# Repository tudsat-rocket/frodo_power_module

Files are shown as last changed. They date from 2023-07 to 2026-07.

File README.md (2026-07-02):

# Power Board

The battery board in our rockets.

### Components

- 3x 3000 mA h Sony VTC6 18650 lithium-ion cells in series

### Usage

| Connector | Purpose |
| --- | --- |
| main switch | + and - needs to be connected to enable the output on HC1, 2, 3 |
| HC1, 2, 3 | Power output |
| circumvent | short + and - to supply power to Vmain without batteries directly from charge voltage |
| Vehicle Bus 1, 2 | Communication and bus power supply |

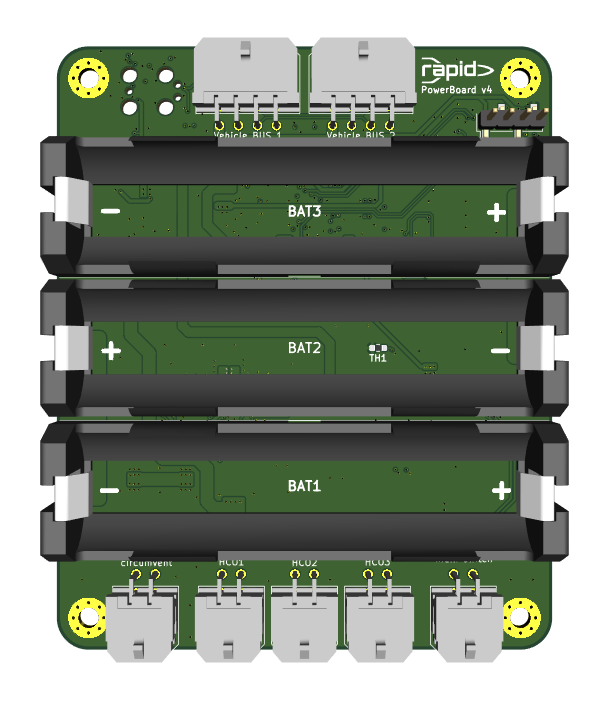
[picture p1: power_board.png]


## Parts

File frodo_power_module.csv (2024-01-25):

Comment | Designator | Footprint | LCSC
470n | C1 | Capacitor_SMD:C_0603_1608Metric | C1623
100n | C2,C6,C8,C11,C14,C15,C16,C17,C18,C19,C20 | Capacitor_SMD:C_0603_1608Metric | C14663
47u | C21,C22,C23,C24,C25,C26,C27,C28 | Capacitor_SMD:C_1206_3216Metric
10u | C3,C5 | Capacitor_SMD:C_1206_3216Metric | C13585
22u | C4 | Capacitor_SMD:C_1206_3216Metric | C12891
1u | C7,C12,C13 | Capacitor_SMD:C_0805_2012Metric | C28323
10p | C9,C10 | Capacitor_SMD:C_0603_1608Metric | C1634
~ | D1 | Diode_SMD:D_SMA | C22452
yellow | D2 | LED_SMD:LED_0603_1608Metric | C72038
red | D3 | LED_SMD:LED_0603_1608Metric | C2286
3V9 | D5,D6 | ZenerDiode:SOD323F_DIO | C444415
1.5A | F1 | Fuse:Fuse_1206_3216Metric
MountingHole_Pad | H1,H2,H3,H4 | MountingHole:MountingHole_3.2mm_M3_Pad_Via | N/A
Keystone 1048 | J1 | frodo_power_module:keystone_1048
SWD Header | J10 | Connector_PinHeader_2.54mm:PinHeader_1x04_P2.54mm_Vertical | N/A
Molex MicroFit 2x3 | J2,J7 | Connector_Molex:Molex_Micro-Fit_3.0_43045-0600_2x03_P3.00mm_Horizontal | C127367
Molex MicroFit 2x2 | J3,J4 | Connector_Molex:Molex_Micro-Fit_3.0_43045-0400_2x02_P3.00mm_Horizontal | C122413
JST-GH | J5,J6 | Connector_JST:JST_GH_SM04B-GHS-TB_1x04-1MP_P1.25mm_Horizontal | C189895
r | JP1,JP2,JP3 | Jumper:SolderJumper-2_P1.3mm_Open_RoundedPad1.0x1.5mm | N/A
BEAD | L1 | Inductor_SMD:L_0603_1608Metric | C1002
120, DNP | R1 | Resistor_SMD:R_0603_1608Metric | C22787
0 | R10 | Resistor_SMD:R_0603_1608Metric | C21189
5m | R13 | Resistor_SMD:R_2512_6332Metric | C723630
100 | R14,R17 | Resistor_SMD:R_0603_1608Metric | C22775
120 | R15 | Resistor_SMD:R_0603_1608Metric | C22787
220 | R16 | Resistor_SMD:R_0603_1608Metric | C22962
5k1 | R20 | Resistor_SMD:R_0603_1608Metric | C23186
1k5 | R25,R26 | Resistor_SMD:R_0603_1608Metric | C22843
22k | R27,R28 | Resistor_SMD:R_0603_1608Metric | C31850
1k | R3,R7,R21,R23 | Resistor_SMD:R_0603_1608Metric | C21190
10k | R4,R18,R19 | Resistor_SMD:R_0603_1608Metric | C25804
100k | R5 | Resistor_SMD:R_0603_1608Metric | C25803
1k8 | R6,R22,R24 | Resistor_SMD:R_0603_1608Metric | C4177
680 | R8 | Resistor_SMD:R_0603_1608Metric | C23228
DNP | R9 | Resistor_SMD:R_0603_1608Metric | N/A
NCU18XH103F6SRB | TH1 | Resistor_SMD:R_0603_1608Metric | C162670
STM32F042F6Px | U1 | Package_SO:TSSOP-20_4.4x6.5mm_P0.65mm | C2969989
L7805 | U2 | Package_TO_SOT_SMD:TO-252-2 | C58069
AZ1117I-3.3 | U3 | Package_TO_SOT_SMD:SOT-223-3_TabPin2 | C92102
BQ25171-Q1 | U4 | Package_SON:Texas_S-PVSON-N10_ThermalVias | C2861221
BQ29200 | U5 | Package_SON:Texas_S-PVSON-N8_ThermalVias | C2865505
MCP2562-E-SN | U6 | Package_SO:SOIC-8_3.9x4.9mm_P1.27mm | C191417
INA213 | U7 | Package_TO_SOT_SMD:SOT-363_SC-70-6 | C129346
8MHz, 12p | Y1 | Crystal:Crystal_SMD_5032-4Pin_5.0x3.2mm | C2149245

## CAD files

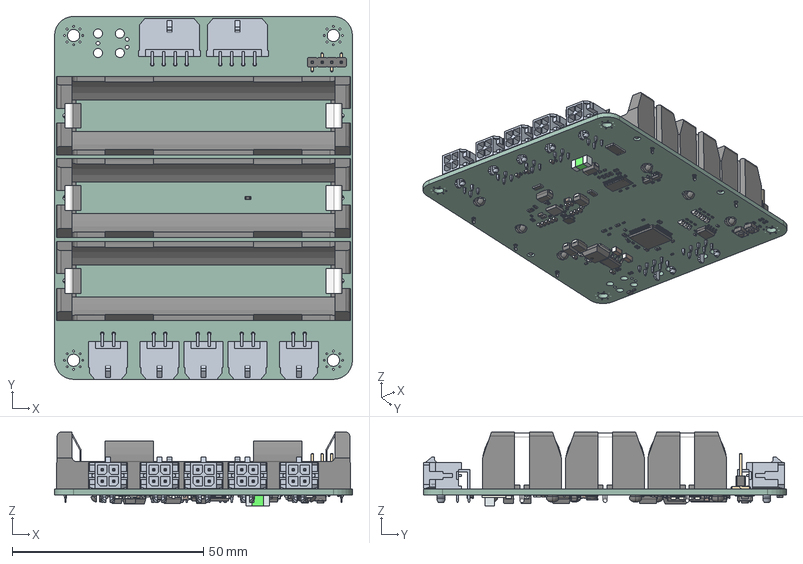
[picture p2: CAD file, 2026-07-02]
power_board.step
78.0 x 95.1 x 19.3 mm
PinHeader_1x04_P254mm_Vertical_SMD_Pin1Left
R_0603_1608Metric x 10
C_0402_1005Metric x 36
LQFP-64_10x10mm_P0.5mm
R_0402_1005Metric x 32
LED_0805_2012Metric x 6
LED_0603_1608Metric x 2
C_0603_1608Metric x 17
C_1206_3216Metric x 2
D_SMA x 5
Fuse_1206_3216Metric x 2
932d09b3-9c39-11ed-93f0-dde97e994e83_part
932d09b4-9c39-11ed-93f0-dde97e994e83_part
932d09b5-9c39-11ed-93f0-dde97e994e83_part
R_0805_2012Metric
SOT-23-6
SOT-23-5
C_0805_2012Metric
term1
term2
R_2512_6332Metric
TSSOP-24_4.4x7.8mm_P0.65mm
SOT-223
BQ25792RQMR
SOT_563
SW_SPST_TS-1088-xR020 x 2
L_Wurth_WE-LQSH-3012
L_0603_1608Metric
SOIC-8_3.9x4.9mm_P1.27mm
power_board_PCB

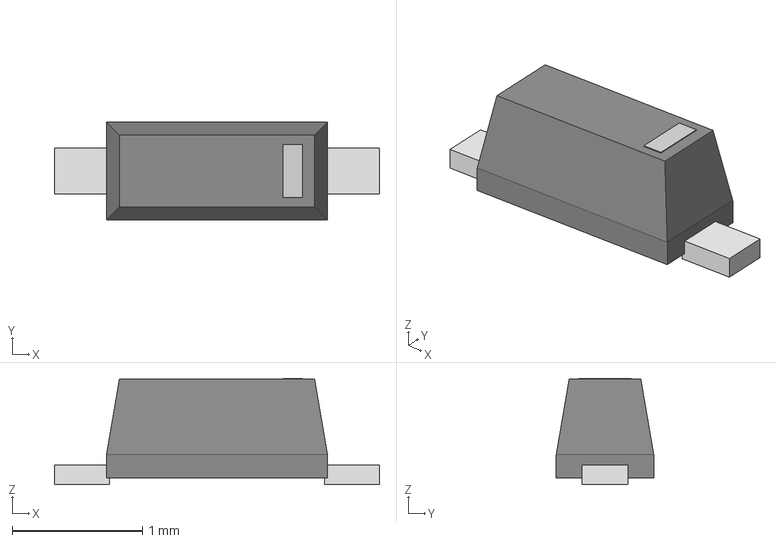
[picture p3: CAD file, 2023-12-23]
SOD323F_DIO.step
2.50 x 0.75 x 0.819 mm

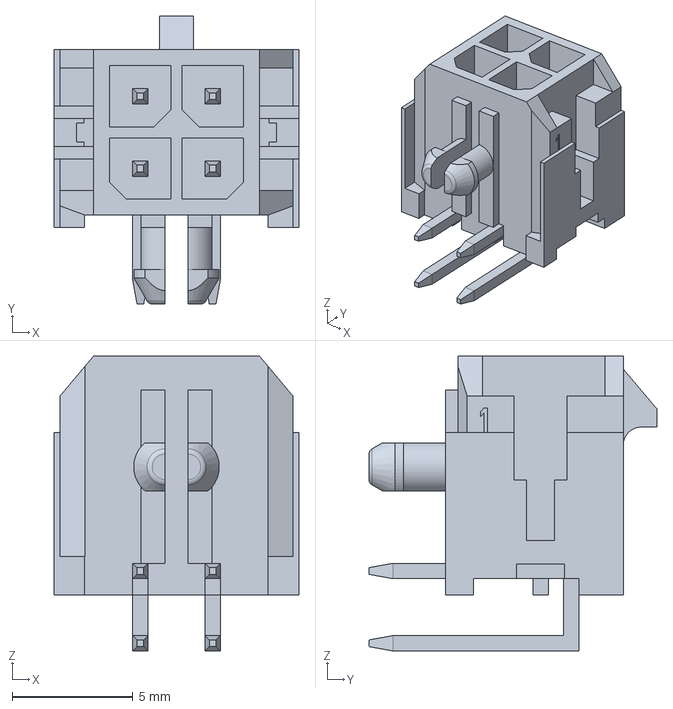
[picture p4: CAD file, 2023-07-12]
430450400.step
10.2 x 11.9 x 12.2 mm

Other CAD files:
power_board.stl

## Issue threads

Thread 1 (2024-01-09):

charge enable and NTC pin swap

wyi5, 2024-01-09:
In revision v2, the charge enable and the NTC pin have been swapped compared to revision v1. This has to be updated in software.

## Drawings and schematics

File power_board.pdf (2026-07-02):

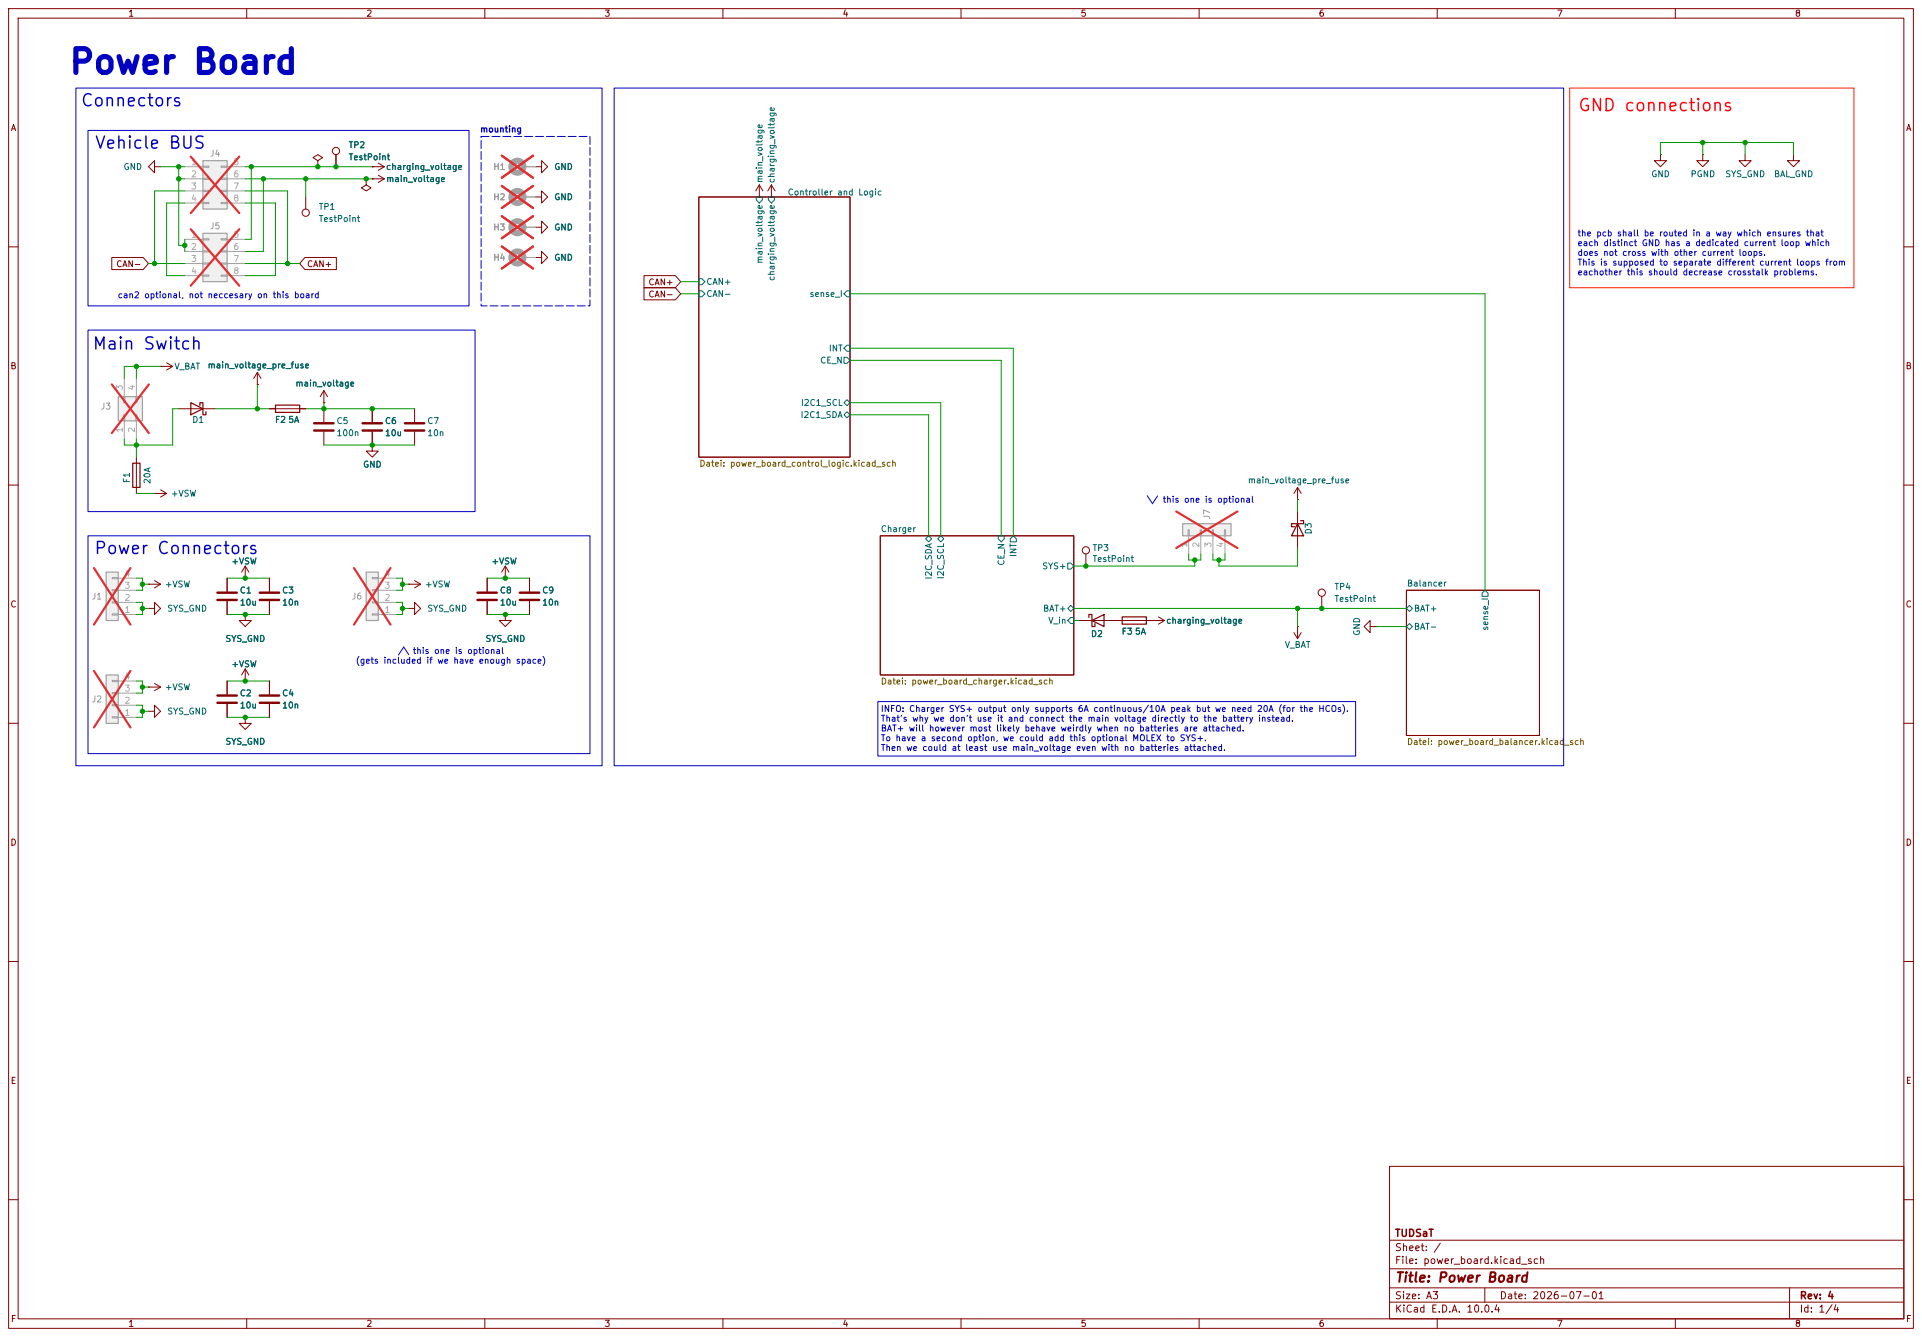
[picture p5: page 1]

can2 optional, not neccesary on this board Vehicle BUS

sense_I Controller and Logic Datei: power_board_control_logic.kicad_sch SYS_GND +VSW

the pcb shall be routed in a way which ensures that each distinct GND has a dedicated current loop which does not cross with other current loops. This is supposed to separate different current loops from eachother this should decrease crosstalk problems.

That's why we don't use it and connect the main voltage directly to the battery instead. BAT+ will however most likely behave weirdly when no batteries are attached. To have a second option, we could add this optional MOLEX to SYS+. Then we could at least use main_voltage even with no batteries attached. Main Switch

\/ this one is optional

/\ this one is optional

(gets included if we have enough space)

INFO: Charger SYS+ output only supports 6A continuous/10A peak but we need 20A (for the HCOs).

Size: A3 | Rev: 4
KiCad E.D.A. 10.0.4 | Id: 1/4 | F Date: 2026-07-01

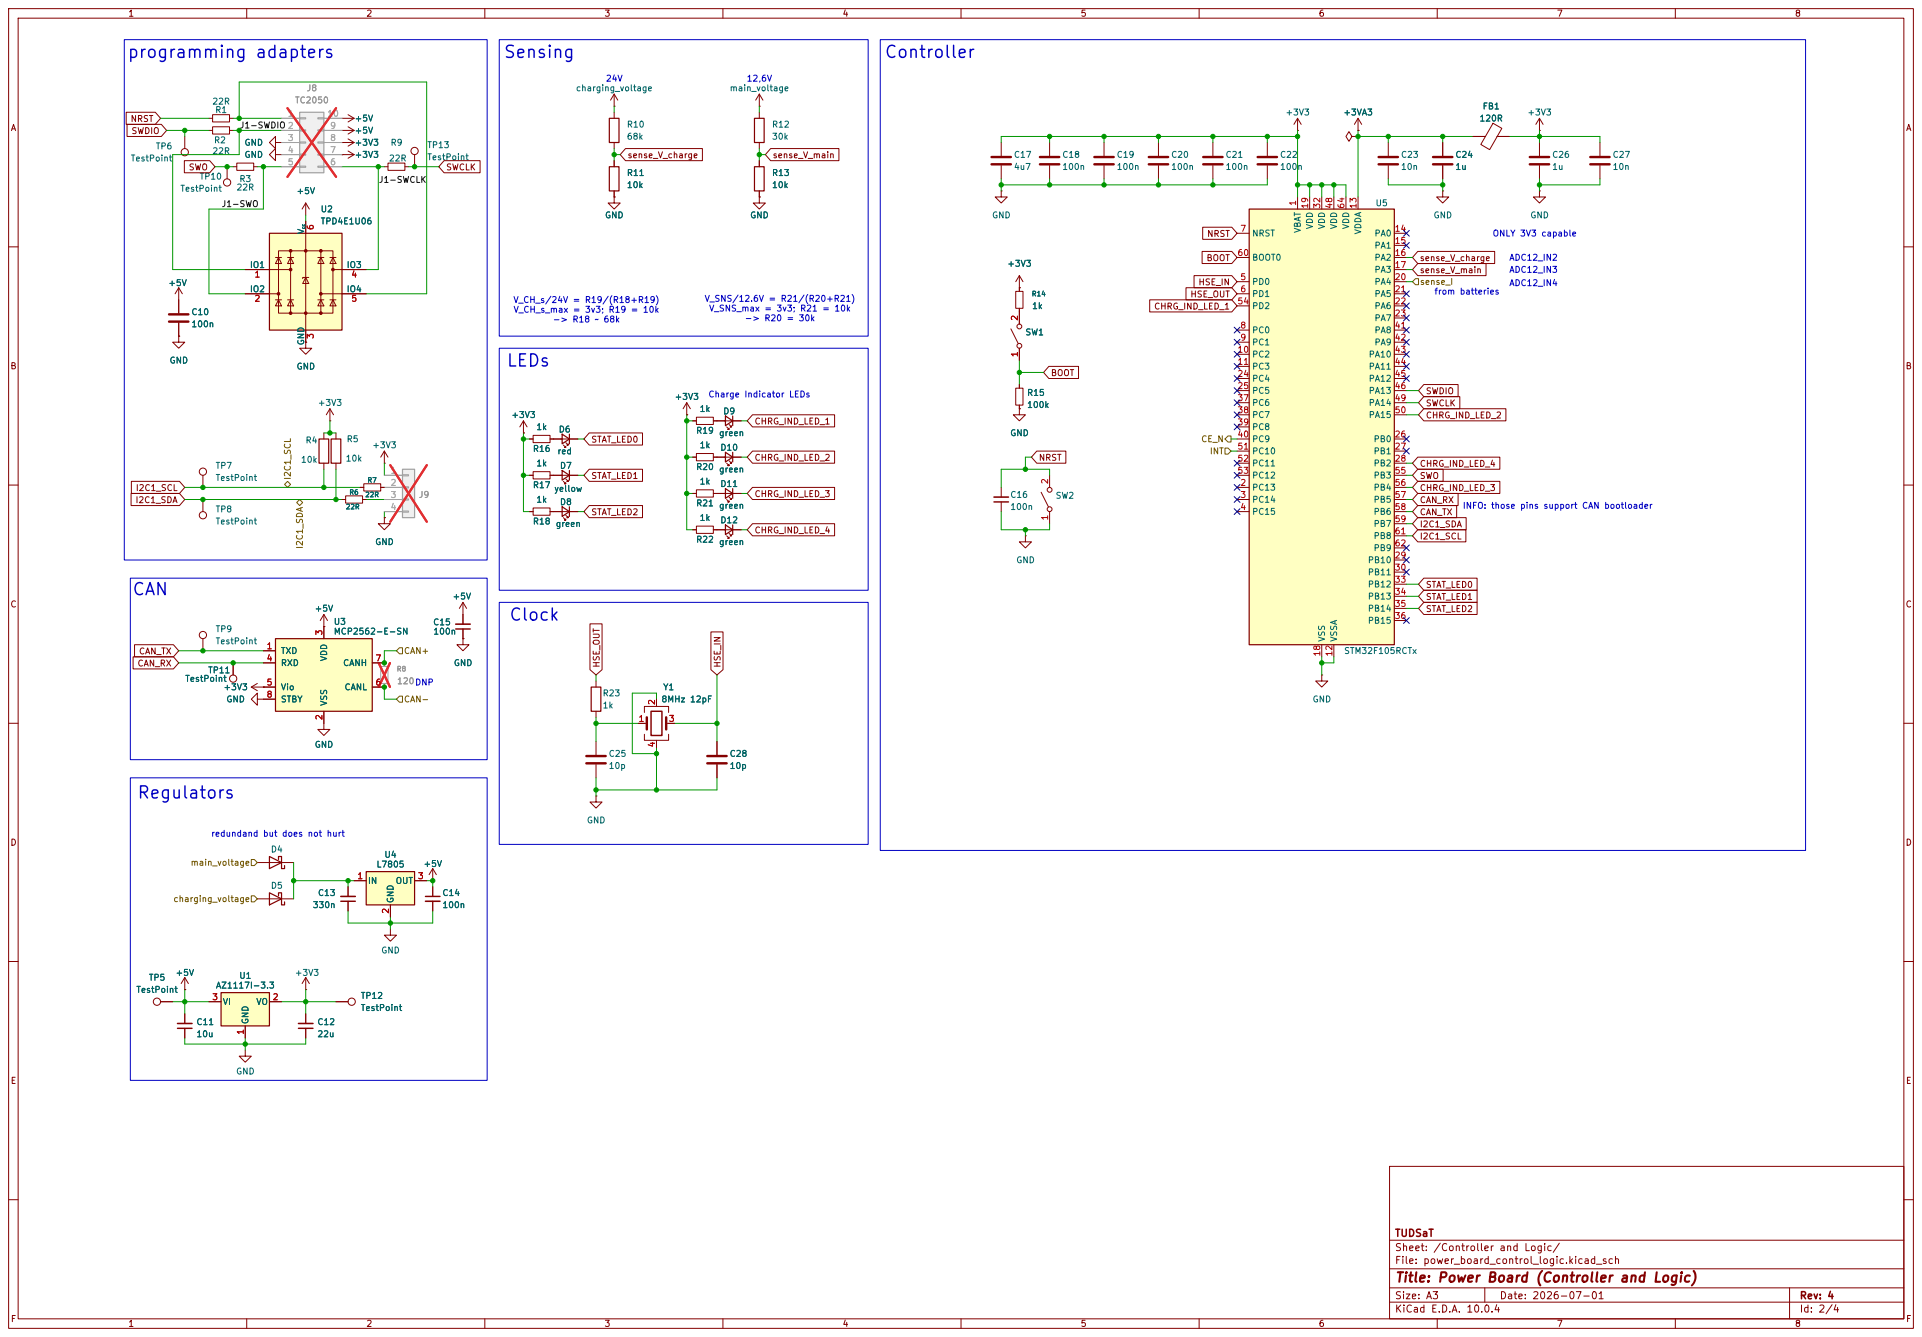
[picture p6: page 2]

from batteries ADC12_IN2 ONLY 3V3 capable

INFO: those pins support CAN bootloader LEDs

redundand but does not hurt

TUDSaT
Sheet: /Controller and Logic/
File: power_board_control_logic.kicad_sch
Title: Power Board (Controller and Logic)

Size: A3 | Rev: 4

F Date: 2026-07-01

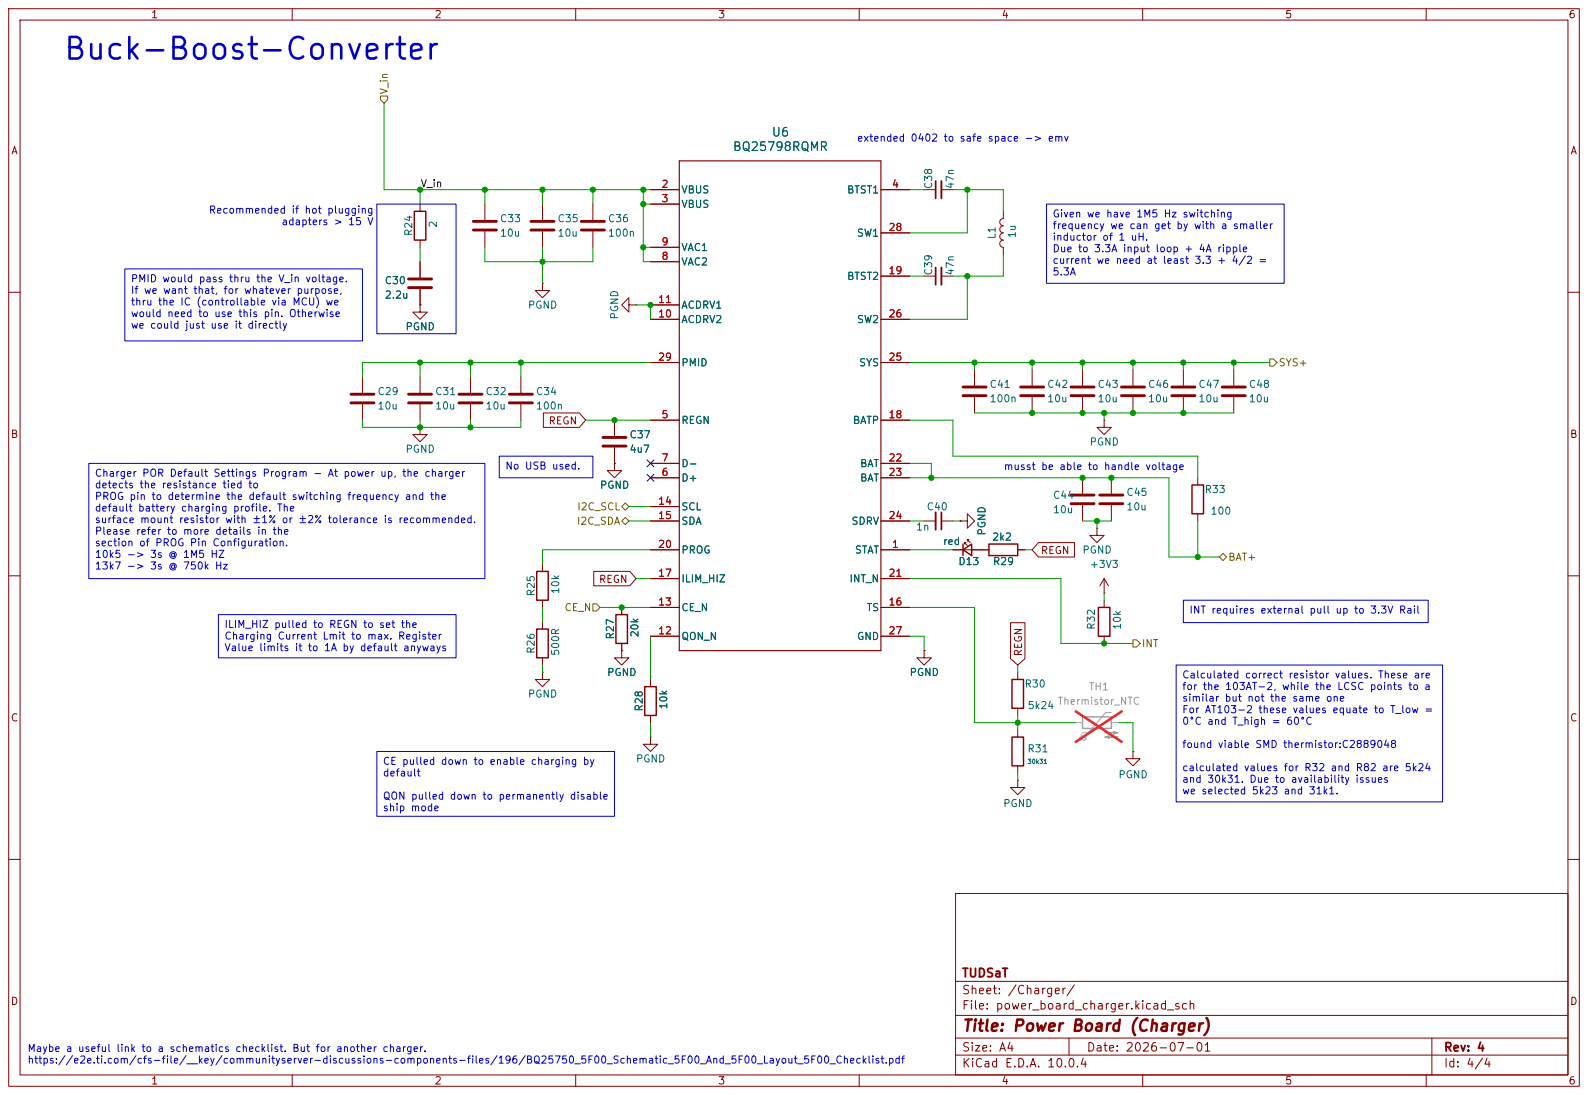
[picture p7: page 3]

5.3A Buck-Boost-Converter
adapters > 15 V Maybe a useful link to a schematics checklist. But for another charger.

extended 0402 to safe space -> emv U6
BQ25798RQMR

V_in PMID would pass thru the V_in voltage.

Recommended if hot plugging

INT requires external pull up to 3.3V Rail Given we have 1M5 Hz switching
frequency we can get by with a smaller
inductor of 1 uH. Due to 3.3A input loop + 4A ripple

current we need at least 3.3 + 4/2 =

If we want that, for whatever purpose, thru the IC (controllable via MCU) we would need to use this pin. Otherwise we could just use it directly

Charger POR Default Settings Program - At power up, the charger detects the resistance tied to PROG pin to determine the default switching frequency and the default battery charging profile. The

surface mount resistor with ±1% or ±2% tolerance is recommended. Please refer to more details in the

section of PROG Pin Configuration. 10k5 -> 3s @ 1M5 HZ

for the 103AT-2, while the LCSC points to a
similar but not the same one
For AT103-2 these values equate to T_low =
0°C and T_high = 60°C

found viable SMD thermistor:C2889048

calculated values for R32 and R82 are 5k24
and 30k31. Due to availability issues we selected 5k23 and 31k1.

Sheet: /Charger/
File: power_board_charger.kicad_sch
Title: Power Board (Charger)

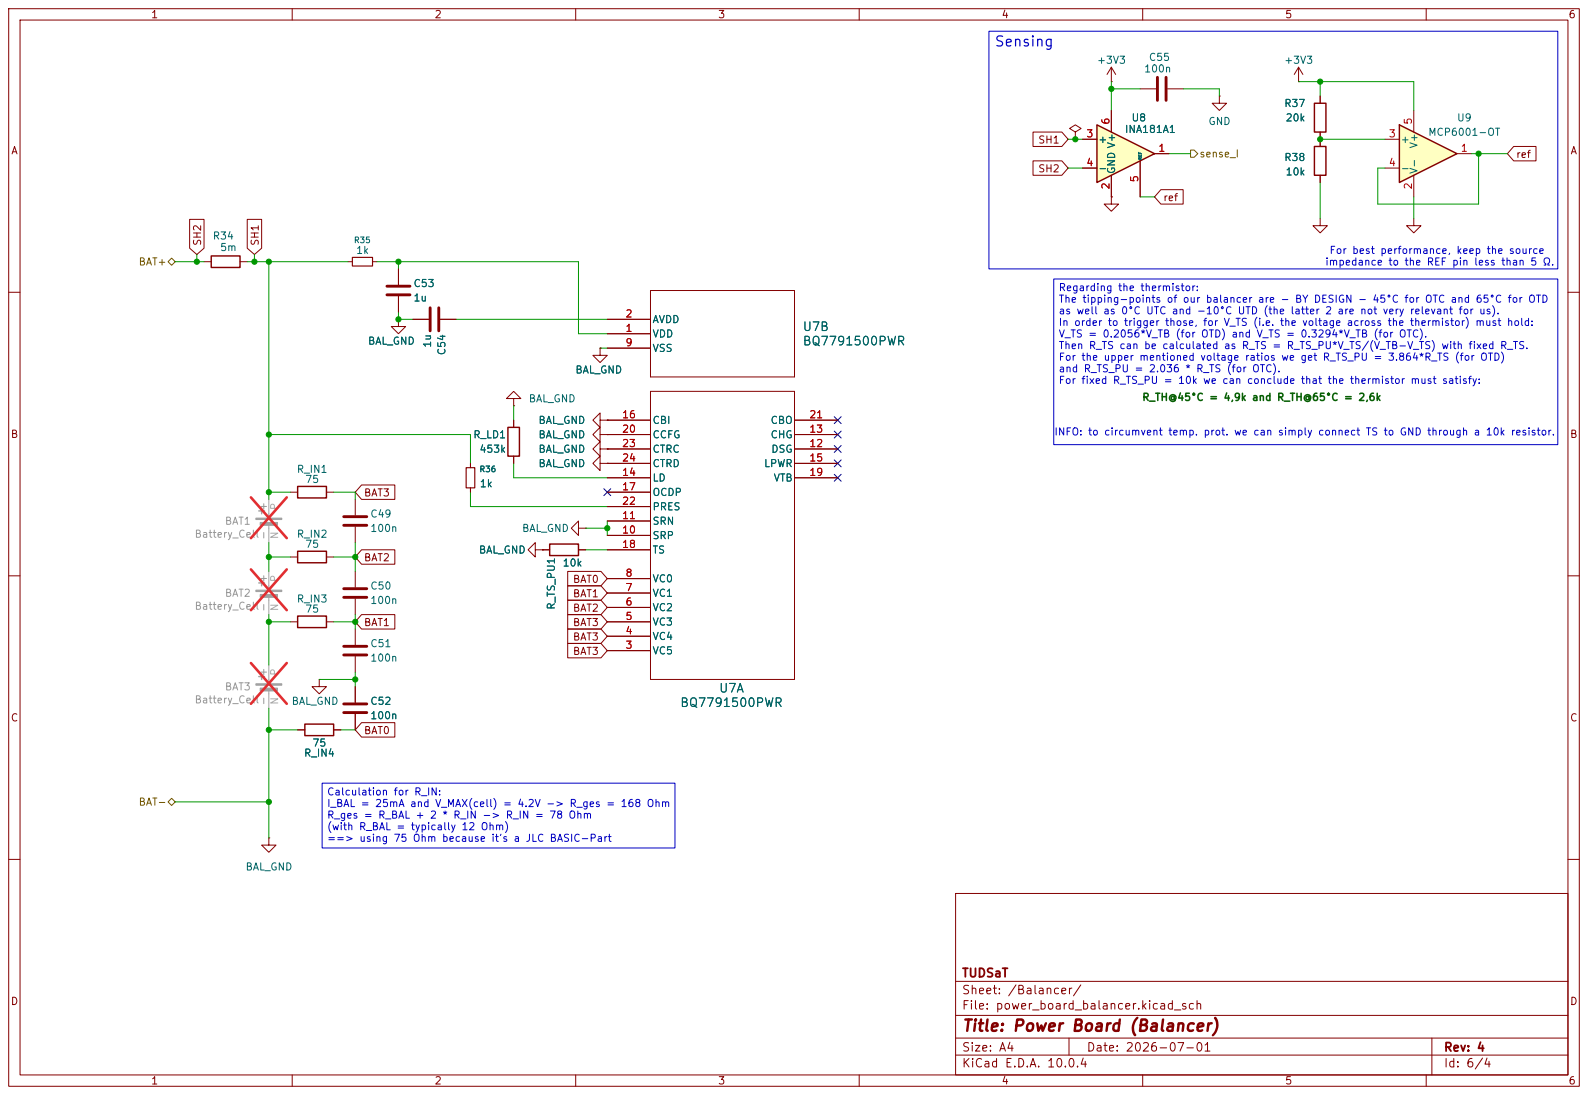
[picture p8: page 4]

INFO: to circumvent temp. prot. we can simply connect TS to GND through a 10k resistor. Sensing

For best performance, keep the source

impedance to the REF pin less than 5 Ω. Regarding the thermistor: The tipping-points of our balancer are - BY DESIGN - 45°C for OTC and 65°C for OTD

as well as 0°C UTC and -10°C UTD (the latter 2 are not very relevant for us).
In order to trigger those, for V_TS (i.e. the voltage across the thermistor) must hold: V_TS = 0.2056*V_TB (for OTD) and V_TS = 0.3294*V_TB (for OTC). Then R_TS can be calculated as R_TS = R_TS_PU*V_TS/(V_TB-V_TS) with fixed R_TS. For the upper mentioned voltage ratios we get R_TS_PU = 3.864*R_TS (for OTD) and R_TS_PU = 2.036 * R_TS (for OTC). For fixed R_TS_PU = 10k we can conclude that the thermistor must satisfy:

Calculation for R_IN:
I_BAL = 25mA and V_MAX(cell) = 4.2V -> R_ges = 168 Ohm
R_ges = R_BAL + 2 * R_IN -> R_IN = 78 Ohm
(with R_BAL = typically 12 Ohm) ==> using 75 Ohm because it's a JLC BASIC-Part

TUDSaT
Sheet: /Balancer/
File: power_board_balancer.kicad_sch
Title: Power Board (Balancer)

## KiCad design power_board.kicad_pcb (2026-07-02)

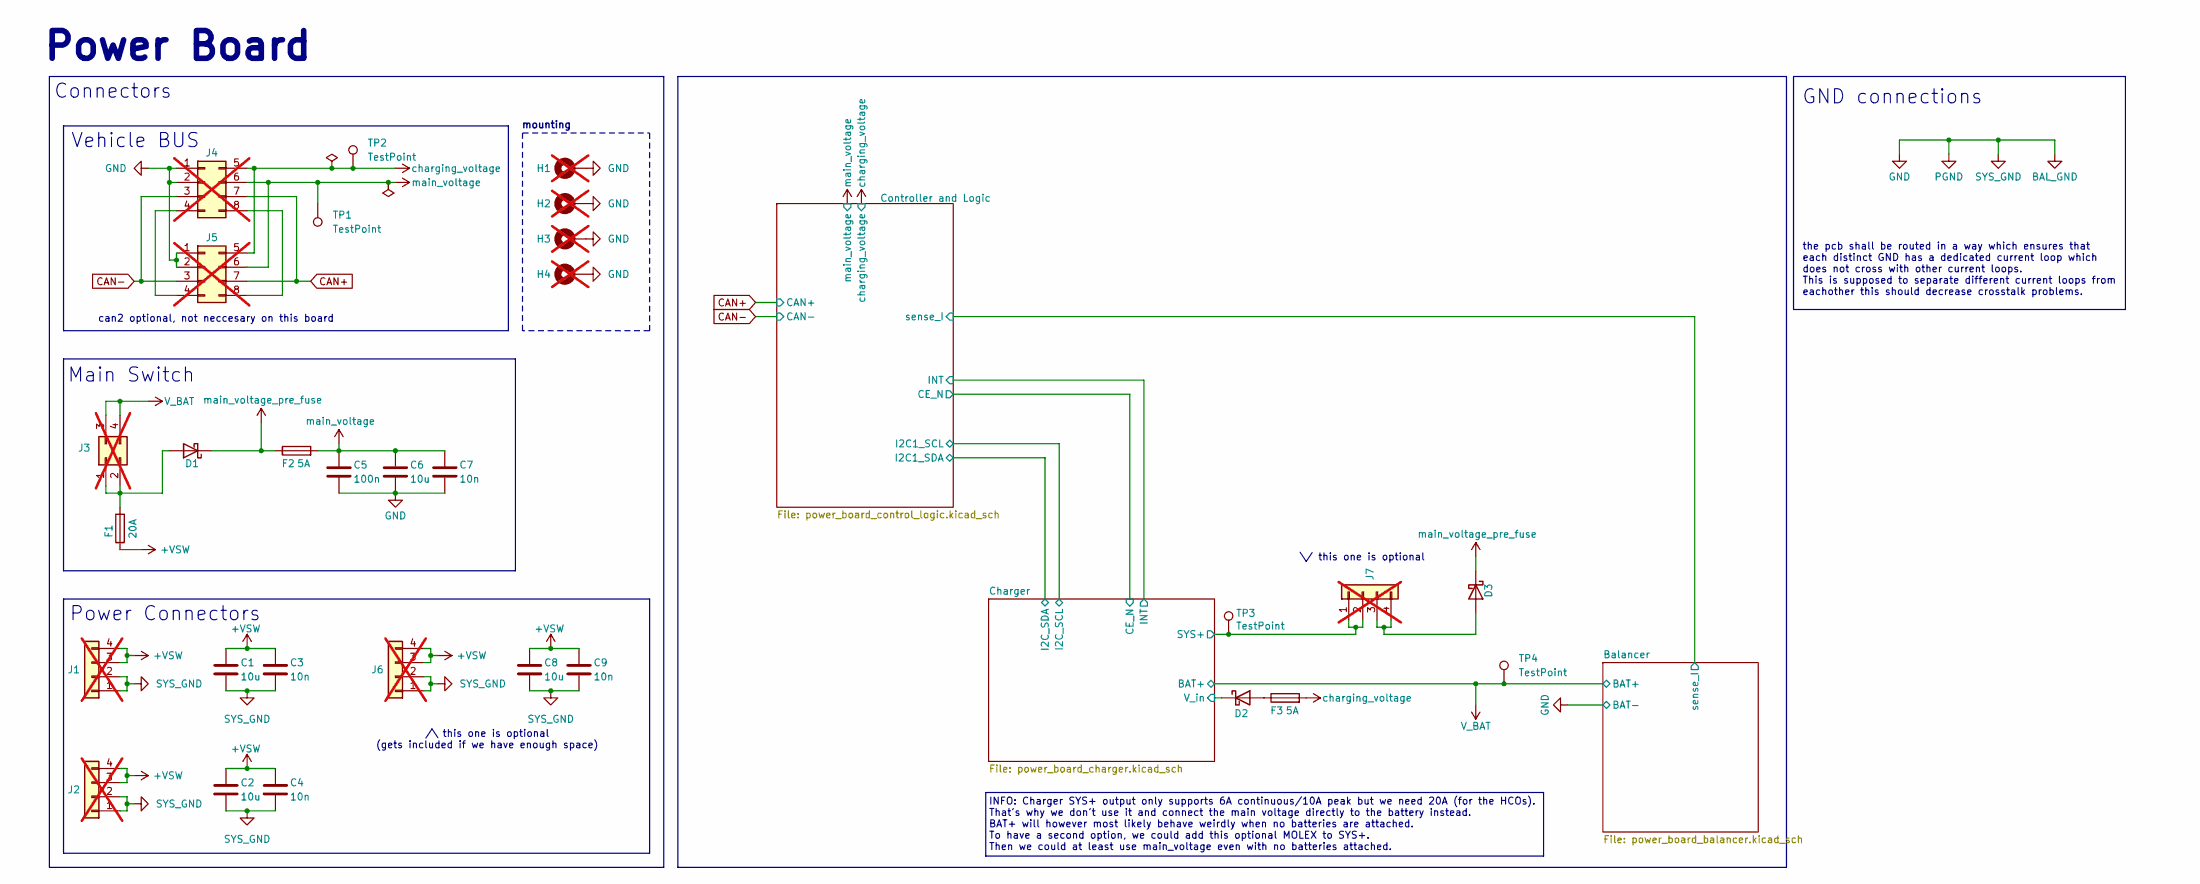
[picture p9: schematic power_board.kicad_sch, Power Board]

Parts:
C1, C2, C6, C8: 10u; C_0603_1608Metric; LCSC C96446
C3, C4, C7, C9: 10n; C_0402_1005Metric; LCSC C15195
C5: 100n; C_0402_1005Metric; LCSC C307331
D1, D2, D3: D_SMA; LCSC C22452
F1: 20A; Fuse_2010_5025Metric_Pad1.52x2.65mm_HandSolder; LCSC C2762483
F2, F3: 5A; Fuse_1206_3216Metric_Pad1.42x1.75mm_HandSolder; LCSC C48332
H1, H2, H3, H4: MountingHole_Pad; MountingHole_3.2mm_M3_Pad_Via; LCSC x; not fitted
J1, J2: Molex MicroFit 2x2; Molex_Micro-Fit_3.0_43045-0400_2x02_P3.00mm_Horizontal; Part# 0430450400; LCSC C122413; not fitted
J3: Molex MicroFit 2x2; Molex_Micro-Fit_3.0_43045-0400_2x02_P3.00mm_Horizontal; LCSC C122413; not fitted
J4, J5: Conn_02x04_Top_Bottom; Molex_Micro-Fit_3.0_43045-0800_2x04_P3.00mm_Horizontal; LCSC x; not fitted
J6, J7: Molex MicroFit 2x2; Molex_Micro-Fit_3.0_43045-0400_2x02_P3.00mm_Horizontal; Part# 0430450400; LCSC# C122413; not fitted
TP1, TP2, TP3, TP4: TestPoint; TestPoint_Pad_D2.0mm

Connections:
+VSW: C1.1, C2.1, C3.1, C4.1, C8.1, C9.1, F1.1, J1.3, J1.4, J2.3, J2.4, J6.3, J6.4
/Charger/SYS+: J7.1, J7.2, TP3.1 (1_1); also elsewhere on the board
/Charger/V_in: D2.1 (K); also elsewhere on the board
BAL_GND: C1.2, C2.2, C3.2, C4.2, C5.2, C6.2, C7.2, C8.2, C9.2, H1.1 (1_1), H2.1 (1_1), H3.1 (1_1), H4.1 (1_1), J1.1, J1.2, J2.1, J2.2, J4.1, J4.2, J5.1, J5.2, J6.1, J6.2; also elsewhere on the board
CAN+: J4.7, J5.7; also elsewhere on the board
CAN-: J4.3, J5.3; also elsewhere on the board
unnamed: D1.2 (A), F1.2, J3.1, J3.2
unnamed: D2.2 (A), F3.1
unnamed: D3.2 (A), J7.3, J7.4
unnamed: J4.4, J5.4
unnamed: J4.8, J5.8
V_BAT: J3.3, J3.4, TP4.1 (1_1); also elsewhere on the board
charging_voltage: F3.2, J4.5, J5.5, TP2.1 (1_1); also elsewhere on the board
main_voltage: C5.1, C6.1, C7.1, F2.2, J4.6, J5.6, TP1.1 (1_1); also elsewhere on the board
main_voltage_pre_fuse: D1.1 (K), D3.1 (K), F2.1

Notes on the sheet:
the pcb shall be routed in a way which ensures that each distinct GND has a dedicated current loop which does not cross with other current loops. This is supposed to separate different current loops from eachother this should decrease crosstalk problems.
Connectors
can2 optional, not neccesary on this board
Vehicle BUS
Main Switch
Power Board
\/ this one is optional
INFO: Charger SYS+ output only supports 6A continuous/10A peak but we need 20A (for the HCOs). That's why we don't use it and connect the main voltage directly to the battery instead. BAT+ will however most likely behave weirdly when no batteries are attached. To have a second option, we could add 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
mounting
/\ this one is optional (gets included if we have enough space)
Power Connectors
GND connections

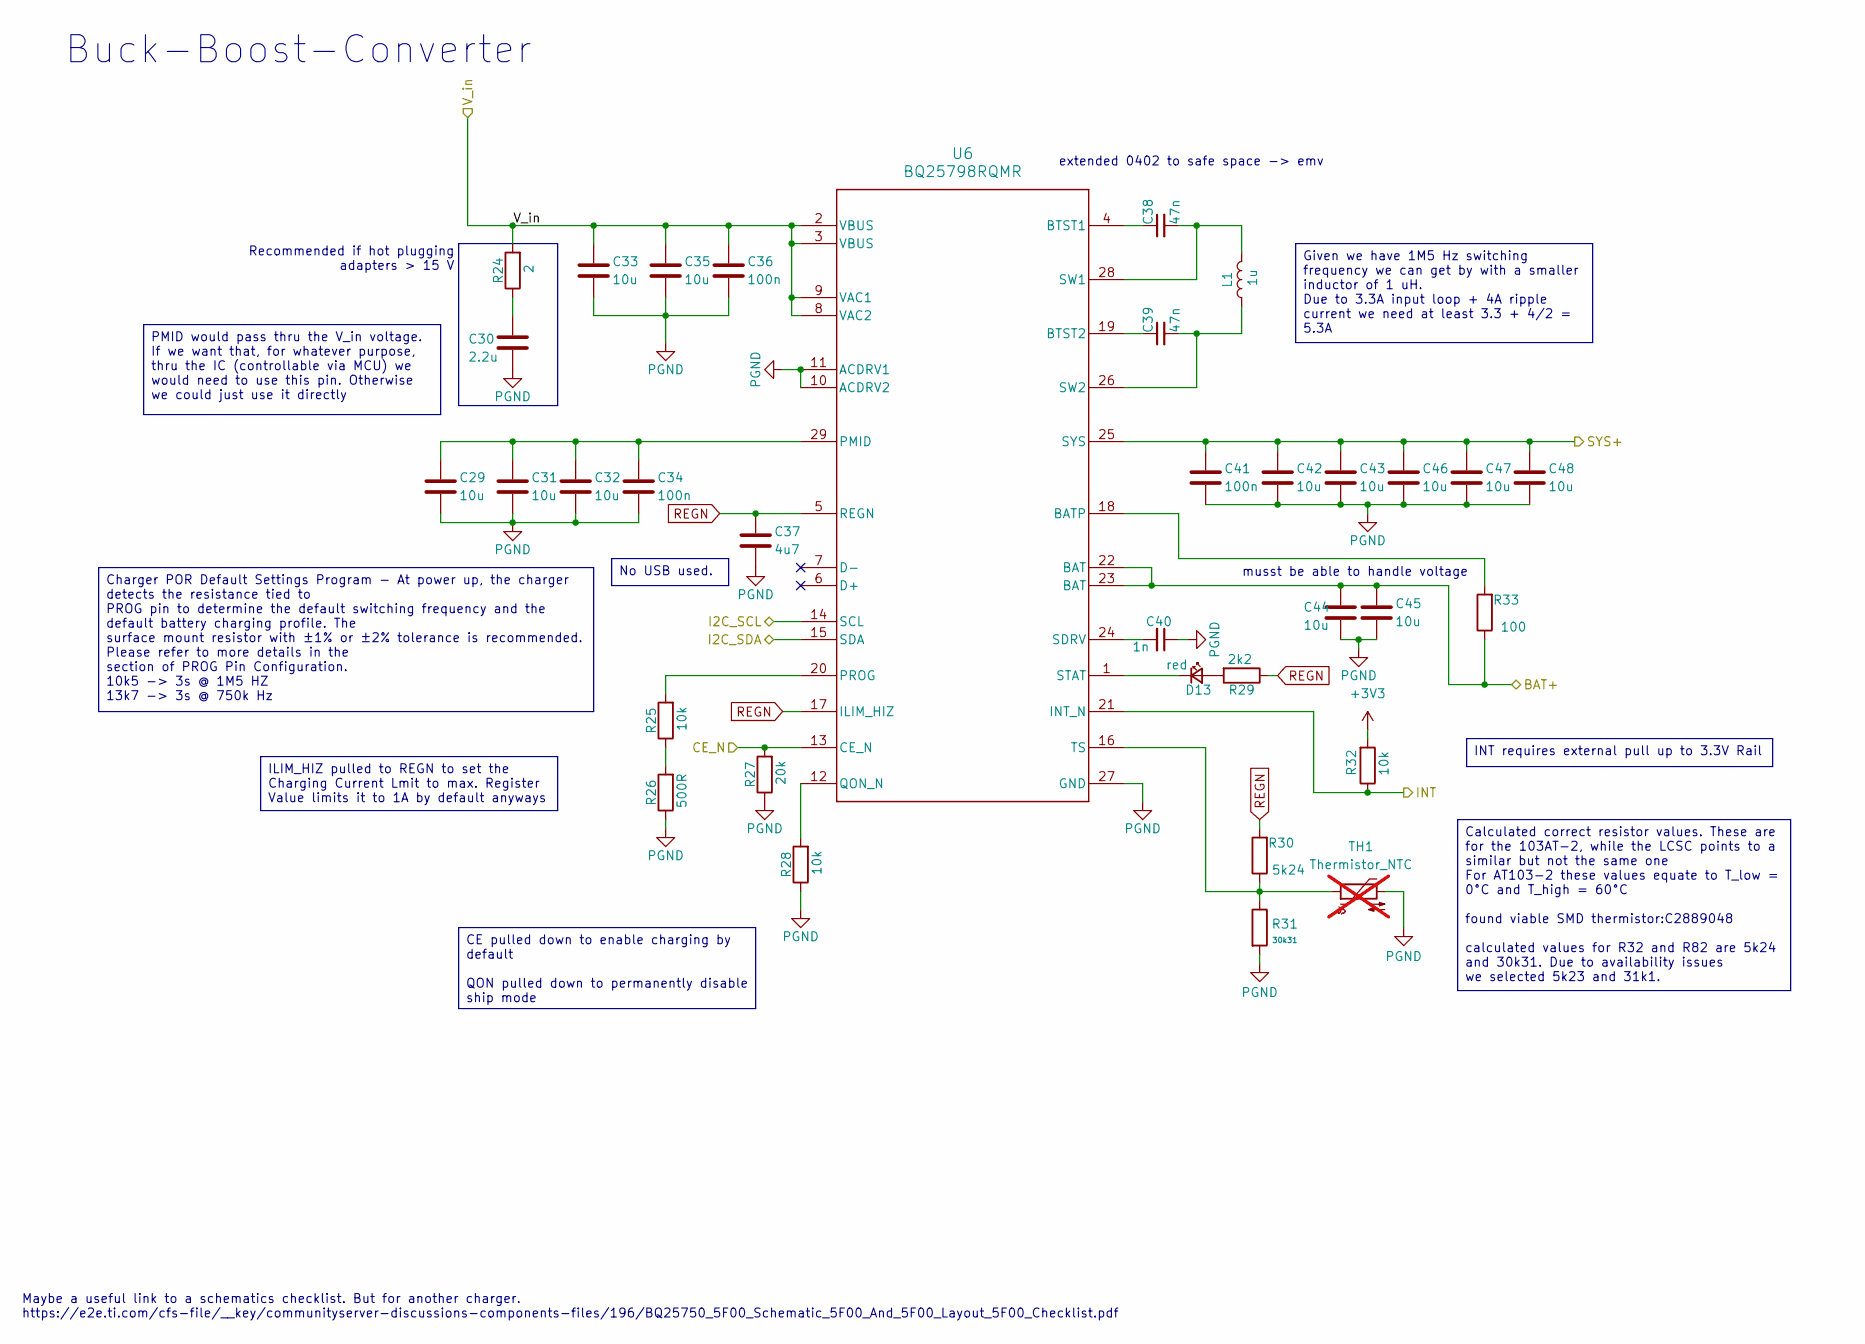
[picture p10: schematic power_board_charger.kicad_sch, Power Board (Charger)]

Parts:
C29, C31, C32, C33, C35, C42, C43, C44, C45, C46, C47, C48: 10u; C_0603_1608Metric; LCSC C96446
C30: 2.2u; C_0805_2012Metric; LCSC C377773
C34, C36, C41: 100n; C_0402_1005Metric; LCSC C307331
C37: 4u7; C_0402_1005Metric; LCSC C23733
C38, C39: 47n; C_0402_1005Metric; LCSC C82219
C40: 1n; C_0402_1005Metric; LCSC C1523
D13: red; LED_0603_1608Metric; LCSC C2286
L1: 1u; L_Wurth_WE-LQSH-3012; LCSC C7423316
R24: 2; R_0603_1608Metric; LCSC C22977
R25, R28, R32: 10k; R_0402_1005Metric; LCSC C25744
R26: 500R; R_0402_1005Metric; LCSC C25123
R27: 20k; R_0603_1608Metric; LCSC C4184
R29: 2k2; R_0402_1005Metric; LCSC C25879
R30: 5k24; R_0603_1608Metric; LCSC C23068
R31: 30k31; R_0805_2012Metric; LCSC C21841
R33: 100; R_0402_1005Metric; LCSC C25076
TH1: Thermistor_NTC; R_0603_1608Metric_Pad0.98x0.95mm_HandSolder; LCSC C2889048; not fitted
U6: BQ25798RQMR; IC_BQ25798RQMR; LCSC C2876593

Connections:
+3V3: R32.2; also elsewhere on the board
/Charger/CE_N: R27.2, U6.13 (CE_N); also elsewhere on the board
/Charger/INT: R32.1, U6.21 (INT_N); also elsewhere on the board
/Charger/SYS+: C41.1, C42.1, C43.1, C46.1, C47.1, C48.1, U6.25 (SYS); also elsewhere on the board
/Charger/V_in: C33.1, C35.1, C36.1, R24.2, U6.2 (VBUS), U6.3 (VBUS), U6.8 (VAC2), U6.9 (VAC1); also elsewhere on the board
BAL_GND: C29.2, C30.2, C31.2, C32.2, C33.2, C34.2, C35.2, C36.2, C37.2, C40.1, C41.2, C42.2, C43.2, C44.2, C45.2, C46.2, C47.2, C48.2, R26.1, R27.1, R28.1, R31.2, TH1.2, U6.10 (ACDRV2), U6.11 (ACDRV1), U6.27 (GND); also elsewhere on the board
I2C1_SCL: U6.14 (SCL); also elsewhere on the board
I2C1_SDA: U6.15 (SDA); also elsewhere on the board
unnamed: C30.1, R24.1
unnamed: D13.2 (A), R29.2
unnamed: D13.1 (K), U6.1 (STAT)
unnamed: R25.1, R26.2
unnamed: R33.2, U6.18 (BATP)
unnamed: C38.1, U6.4 (BTST1)
unnamed: C39.1, U6.19 (BTST2)
unnamed: C29.1, C31.1, C32.1, C34.1, U6.29 (PMID)
unnamed: R25.2, U6.20 (PROG)
unnamed: R28.2, U6.12 (QON_N)
unnamed: C40.2, U6.24 (SDRV)
unnamed: C38.2, L1.2, U6.28 (SW1)
unnamed: C39.2, L1.1, U6.26 (SW2)
unnamed: R30.1, R31.1, TH1.1, U6.16 (TS)
REGN: C37.1, R29.1, R30.2, U6.5 (REGN), U6.17 (ILIM_HIZ)
V_BAT: C44.1, C45.1, R33.1, U6.22 (BAT), U6.23 (BAT); also elsewhere on the board

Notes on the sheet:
extended 0402 to safe space -> emv
Buck-Boost-Converter
Recommended if hot plugging adapters > 15 V
Maybe a useful link to a schematics checklist. But for another charger. https://e2e.ti.com/cfs-file/__key/communityserver-discussions-components-files/196/BQ25750_5F00_Schematic_5F00_And_5F00_Layout_5F00_Checklist.pdf
musst be able to handle voltage
ILIM_HIZ pulled to REGN to set the Charging Current Lmit to max. Register Value limits it to 1A by default anyways
Given we have 1M5 Hz switching frequency we can get by with a smaller inductor of 1 uH. Due to 3.3A input loop + 4A ripple current we need at least 3.3 + 4/2 = 5.3A
INT requires external pull up to 3.3V Rail
Calculated correct resistor values. These are for the 103AT-2, while the LCSC points to a similar but not the same one For AT103-2 these values equate to T_low = 0°C and T_high = 60°C found viable SMD thermistor:C2889048 calculated values for R32 and R82 are 5k24 and 30k31. Due to availability issu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
PMID would pass thru the V_in voltage. If we want that, for whatever purpose, thru the IC (controllable via MCU) we would need to use this pin. Otherwise we could just use it directly
CE pulled down to enable charging by default QON pulled down to permanently disable ship mode
No USB used.
Charger POR Default Settings Program - At power up, the charger detects the resistance tied to PROG pin to determine the default switching frequency and the default battery charging profile. The surface mount resistor with ±1% or ±2% tolerance is recommended. Please refer to more details in the sec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

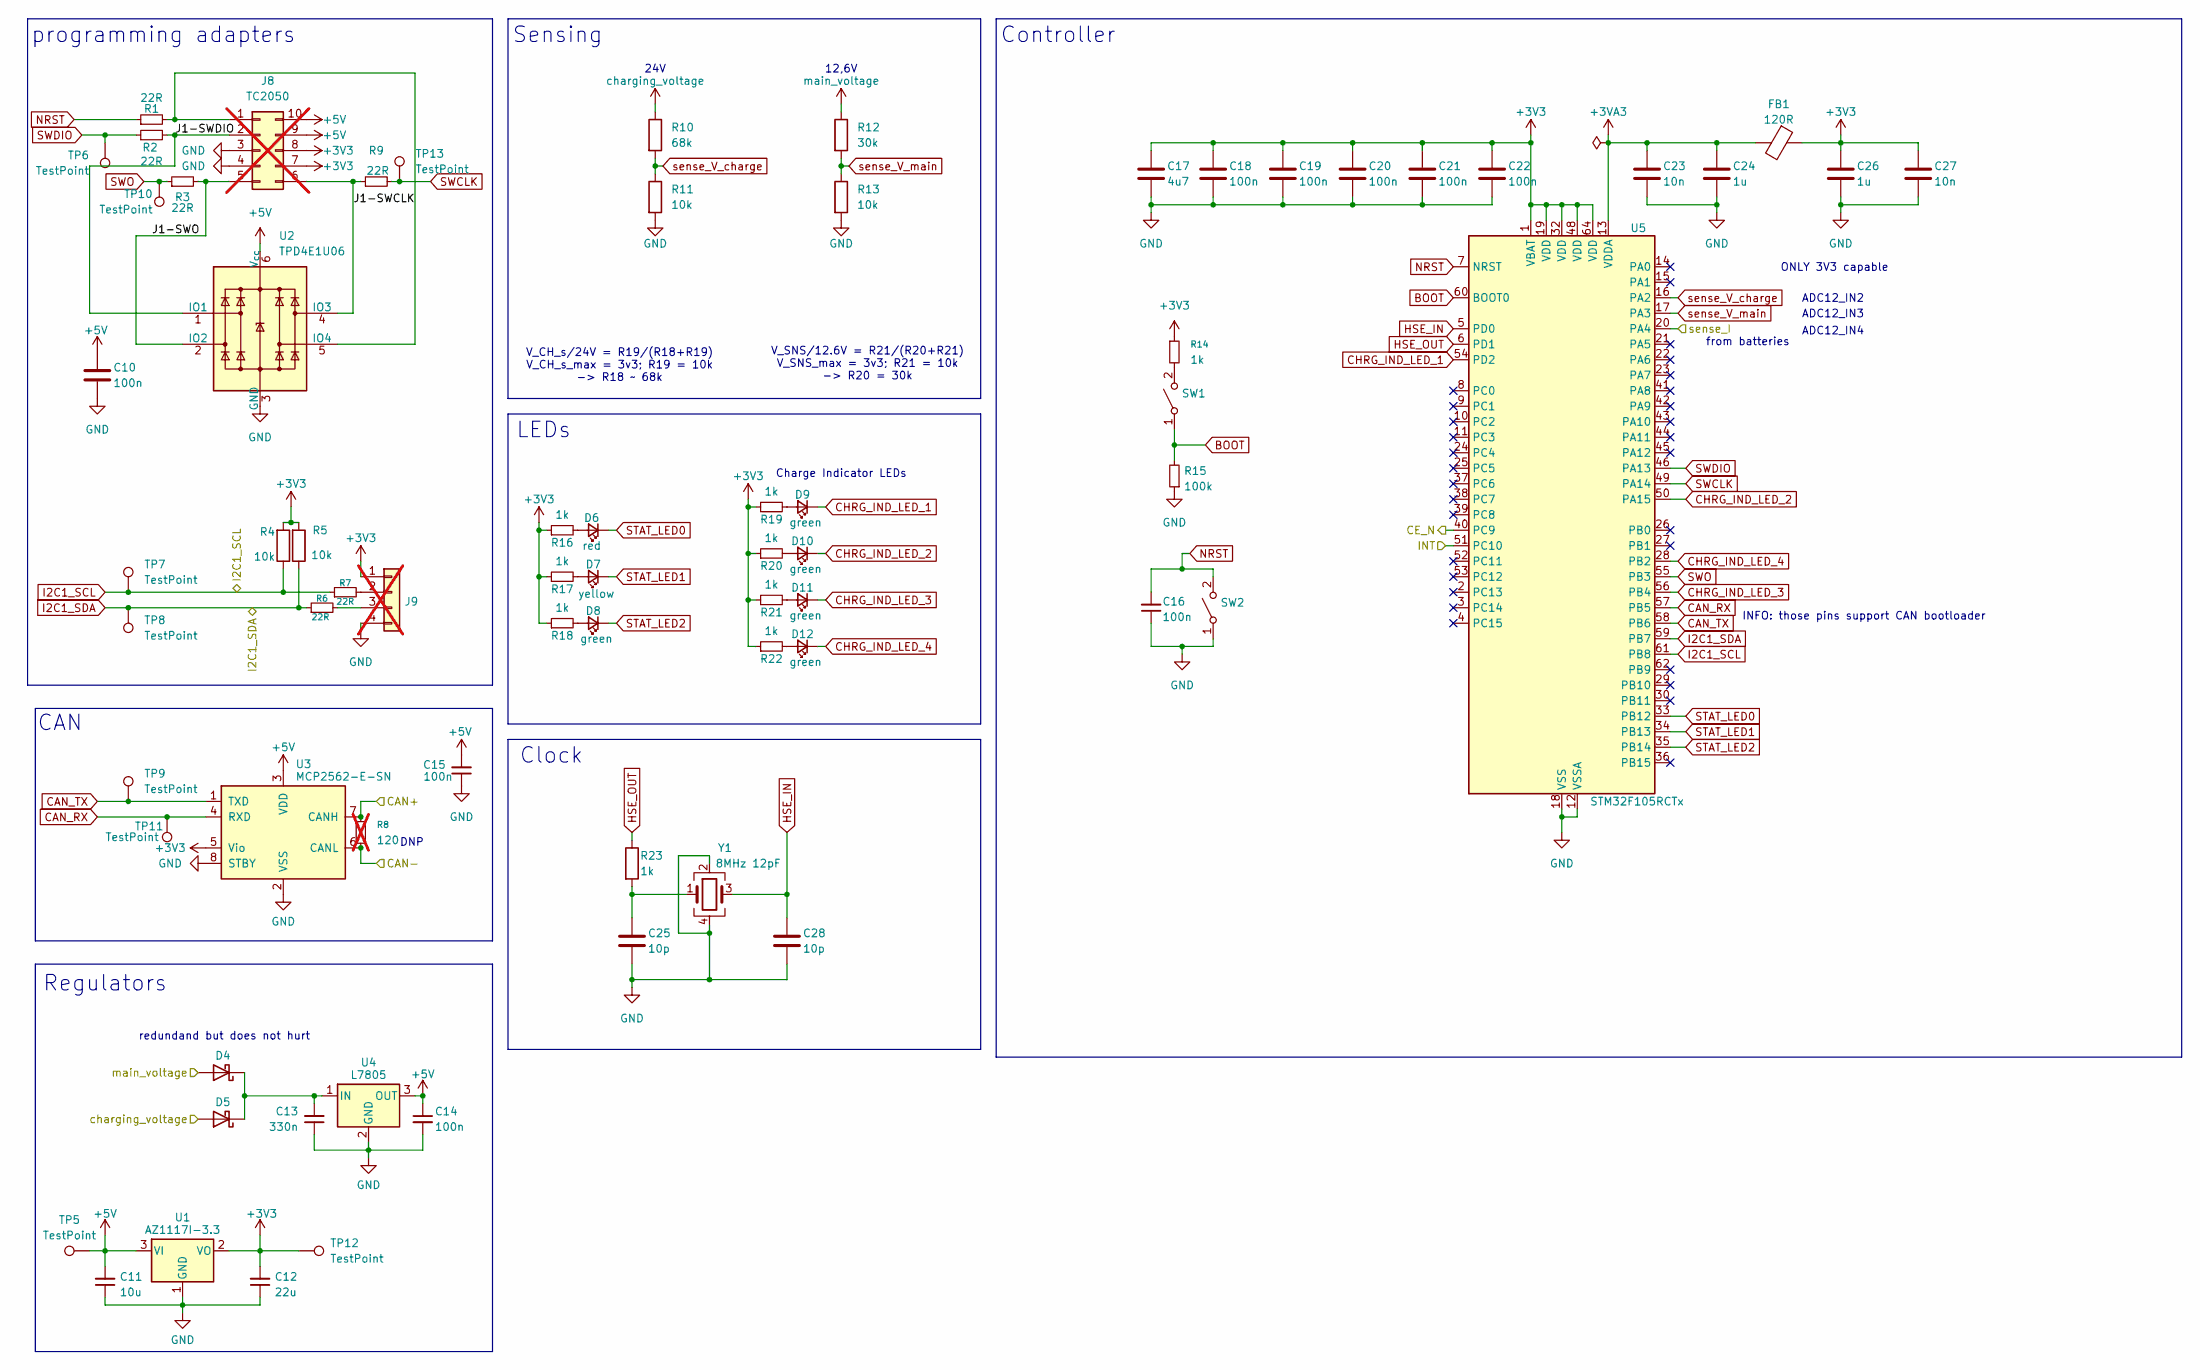
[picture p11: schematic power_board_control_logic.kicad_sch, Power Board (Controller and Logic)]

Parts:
C10, C15, C18, C19, C20, C21, C22: 100n; C_0402_1005Metric; LCSC C307331
C11: 10u; C_1206_3216Metric; Part# CL31A106KBHNNNE; LCSC C13585
C12: 22u; C_1206_3216Metric; Part# CL31A226KAHNNNE; LCSC C12891
C13: 330n; C_0603_1608Metric; Part# CL10B474KA8NNNC; LCSC C1615
C14: 100n; C_0402_1005Metric; Part# CC0603KRX7R9BB104; LCSC C307331
C16: 100n; C_0402_1005Metric; Part# CL10B104KB8NNNC; LCSC C307331
C17: 4u7; C_0402_1005Metric; LCSC C23733
C23, C27: 10n; C_0402_1005Metric; LCSC C15195
C24, C26: 1u; C_0402_1005Metric; LCSC C52923
C25, C28: 10p; C_0402_1005Metric; LCSC C32949
D4, D5: D_SMA; LCSC C22452
D6: red; LED_0603_1608Metric; LCSC C2286
D7: yellow; LED_0805_2012Metric; LCSC C2296
D8, D9, D10, D11, D12: green; LED_0805_2012Metric; LCSC C2297
FB1: 120R; L_0603_1608Metric; Part# BLM18PG121SN1D; LCSC C14709
J8: TC2050; Tag-Connect_TC2050-IDC-FP_2x05_P1.27mm_Vertical; LCSC x; not fitted
J9: SWD Header; PinHeader_1x04_P2.54mm_Vertical_SMD_Pin1Left; LCSC x; not fitted
R1, R2, R3, R9: 22R; R_0402_1005Metric; Part# RC0603FR-0710KL; LCSC C25092
R4, R5, R11, R13: 10k; R_0402_1005Metric; LCSC C25744
R6, R7: 22R; R_0402_1005Metric; Part# RC0603FR-0722RL; LCSC C25092
R8: 120; C_0402_1005Metric; LCSC C25079; not fitted
R10: 68k; R_0603_1608Metric; LCSC C23231
R12: 30k; R_0603_1608Metric; LCSC C22984
R14, R16, R17, R18, R19, R20, R21, R22, R23: 1k; R_0402_1005Metric; LCSC C11702
R15: 100k; R_0402_1005Metric; Part# RC0603FR-0710KL; LCSC C25741
SW1, SW2: SW_SPST_TS-1088-xR020; LCSC C720477
TP5, TP6, TP7, TP8, TP9, TP10, TP11, TP12, TP13: TestPoint; TestPoint_Pad_D2.0mm
U1: AZ1117I-3.3; SOT-223-3_TabPin2; Part# AZ1117CH-3.3TRG1; LCSC C92102
U2: TPD4E1U06; SOT-563; LCSC C527516
U3: MCP2562-E-SN; SOIC-8_3.9x4.9mm_P1.27mm; Part# MCP2562-H/SN; DigiKey# MCP2562-H/SN
U4: L7805; TO-252-2; Part# L78M05ABDT-TR; LCSC C58069
U5: STM32F105RCTx; LQFP-64_10x10mm_P0.5mm; LCSC C8345
Y1: 8MHz 12pF; Crystal_SMD_5032-4Pin_5.0x3.2mm; Part# 5TJ480000NYLBC; LCSC C2149245

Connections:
+3V3: C12.2, C17.1, C18.1, C19.1, C20.1, C21.1, C22.1, C26.1, C27.1, FB1.1, J8.7, J8.8, J9.1, R4.2, R5.2, R14.1, R16.1, R17.1, R18.1, R19.1, R20.1, R21.1, R22.1, TP12.1 (1_1), U1.2 (VO), U3.5 (Vio), U5.1 (VBAT), U5.19 (VDD), U5.32 (VDD), U5.48 (VDD), U5.64 (VDD); also elsewhere on the board
+3VA3: C23.1, C24.1, FB1.2, U5.13 (VDDA)
+5V: C10.1, C11.2, C14.1, C15.2, J8.9, J8.10, TP5.1 (1_1), U1.3 (VI), U2.6 (V_{cc}), U3.3 (VDD), U4.3 (OUT)
/Balancer/sense_I: U5.20 (PA4); also elsewhere on the board
/Charger/CE_N: U5.40 (PC9); also elsewhere on the board
/Charger/INT: U5.51 (PC10); also elsewhere on the board
/Controller and Logic/J1-SWCLK: J8.6, R9.1, U2.4 (IO3)
/Controller and Logic/J1-SWDIO: J8.2, R2.2, U2.1 (IO1)
/Controller and Logic/J1-SWO: J8.5, R3.2, U2.2 (IO2)
BAL_GND: C10.2, C11.1, C12.1, C13.1, C14.2, C15.1, C16.1, C17.2, C18.2, C19.2, C20.2, C21.2, C22.2, C23.2, C24.2, C25.2, C26.2, C27.2, C28.2, J8.3, J8.4, J9.4, R11.2, R13.2, R15.1, SW2.1 (A), U1.1 (GND), U2.3 (GND), U3.2 (VSS), U3.8 (STBY), U4.2 (GND), U5.12 (VSSA), U5.18 (VSS), U5.31 (VSS), U5.47 (VSS), U5.63 (VSS), Y1.2, Y1.4; also elsewhere on the board
BOOT: R15.2, SW1.1 (A), U5.60 (BOOT0)
CAN+: R8.1, U3.7 (CANH); also elsewhere on the board
CAN-: R8.2, U3.6 (CANL); also elsewhere on the board
CAN_RX: TP11.1 (1_1), U3.4 (RXD), U5.57 (PB5)
CAN_TX: TP9.1 (1_1), U3.1 (TXD), U5.58 (PB6)
CHRG_IND_LED_1: D9.1 (K), U5.54 (PD2)
CHRG_IND_LED_2: D10.1 (K), U5.50 (PA15)
CHRG_IND_LED_3: D11.1 (K), U5.56 (PB4)
CHRG_IND_LED_4: D12.1 (K), U5.28 (PB2)
HSE_IN: C28.1, U5.5 (PD0), Y1.3
HSE_OUT: R23.1, U5.6 (PD1)
I2C1_SCL: R4.1, R7.1, TP7.1 (1_1), U5.61 (PB8); also elsewhere on the board
I2C1_SDA: R5.1, R6.1, TP8.1 (1_1), U5.59 (PB7); also elsewhere on the board
NRST: C16.2, R1.1, SW2.2 (B), U5.7 (NRST)
unnamed: C25.1, R23.2, Y1.1
unnamed: C13.2, D4.1 (K), D5.1 (K), U4.1 (IN)
unnamed: D6.2 (A), R16.2
unnamed: D7.2 (A), R17.2
unnamed: D8.2 (A), R18.2
unnamed: D9.2 (A), R19.2
unnamed: D10.2 (A), R20.2
unnamed: D11.2 (A), R21.2
unnamed: D12.2 (A), R22.2
unnamed: J8.1, R1.2, U2.5 (IO4)
unnamed: J9.2, R7.2
unnamed: J9.3, R6.2
unnamed: R14.2, SW1.2 (B)
STAT_LED0: D6.1 (K), U5.33 (PB12)
STAT_LED1: D7.1 (K), U5.34 (PB13)
STAT_LED2: D8.1 (K), U5.35 (PB14)
SWCLK: R9.2, TP13.1 (1_1), U5.49 (PA14)
SWDIO: R2.1, TP6.1 (1_1), U5.46 (PA13)
SWO: R3.1, TP10.1 (1_1), U5.55 (PB3)
charging_voltage: D5.2 (A), R10.1; also elsewhere on the board
main_voltage: D4.2 (A), R12.1; also elsewhere on the board
sense_V_charge: R10.2, R11.1, U5.16 (PA2)
sense_V_main: R12.2, R13.1, U5.17 (PA3)

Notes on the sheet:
Clock
INFO: those pins support CAN bootloader
Controller
from batteries
Sensing
Charge Indicator LEDs
Regulators
redundand but does not hurt
V_SNS/12.6V = R21/(R20+R21) V_SNS_max = 3v3; R21 = 10k -> R20 = 30k
LEDs
ADC12_IN3
ADC12_IN4
programming adapters
ONLY 3V3 capable
12,6V
ADC12_IN2
DNP
CAN
24V
V_CH_s/24V = R19/(R18+R19) V_CH_s_max = 3v3; R19 = 10k -> R18 ~ 68k

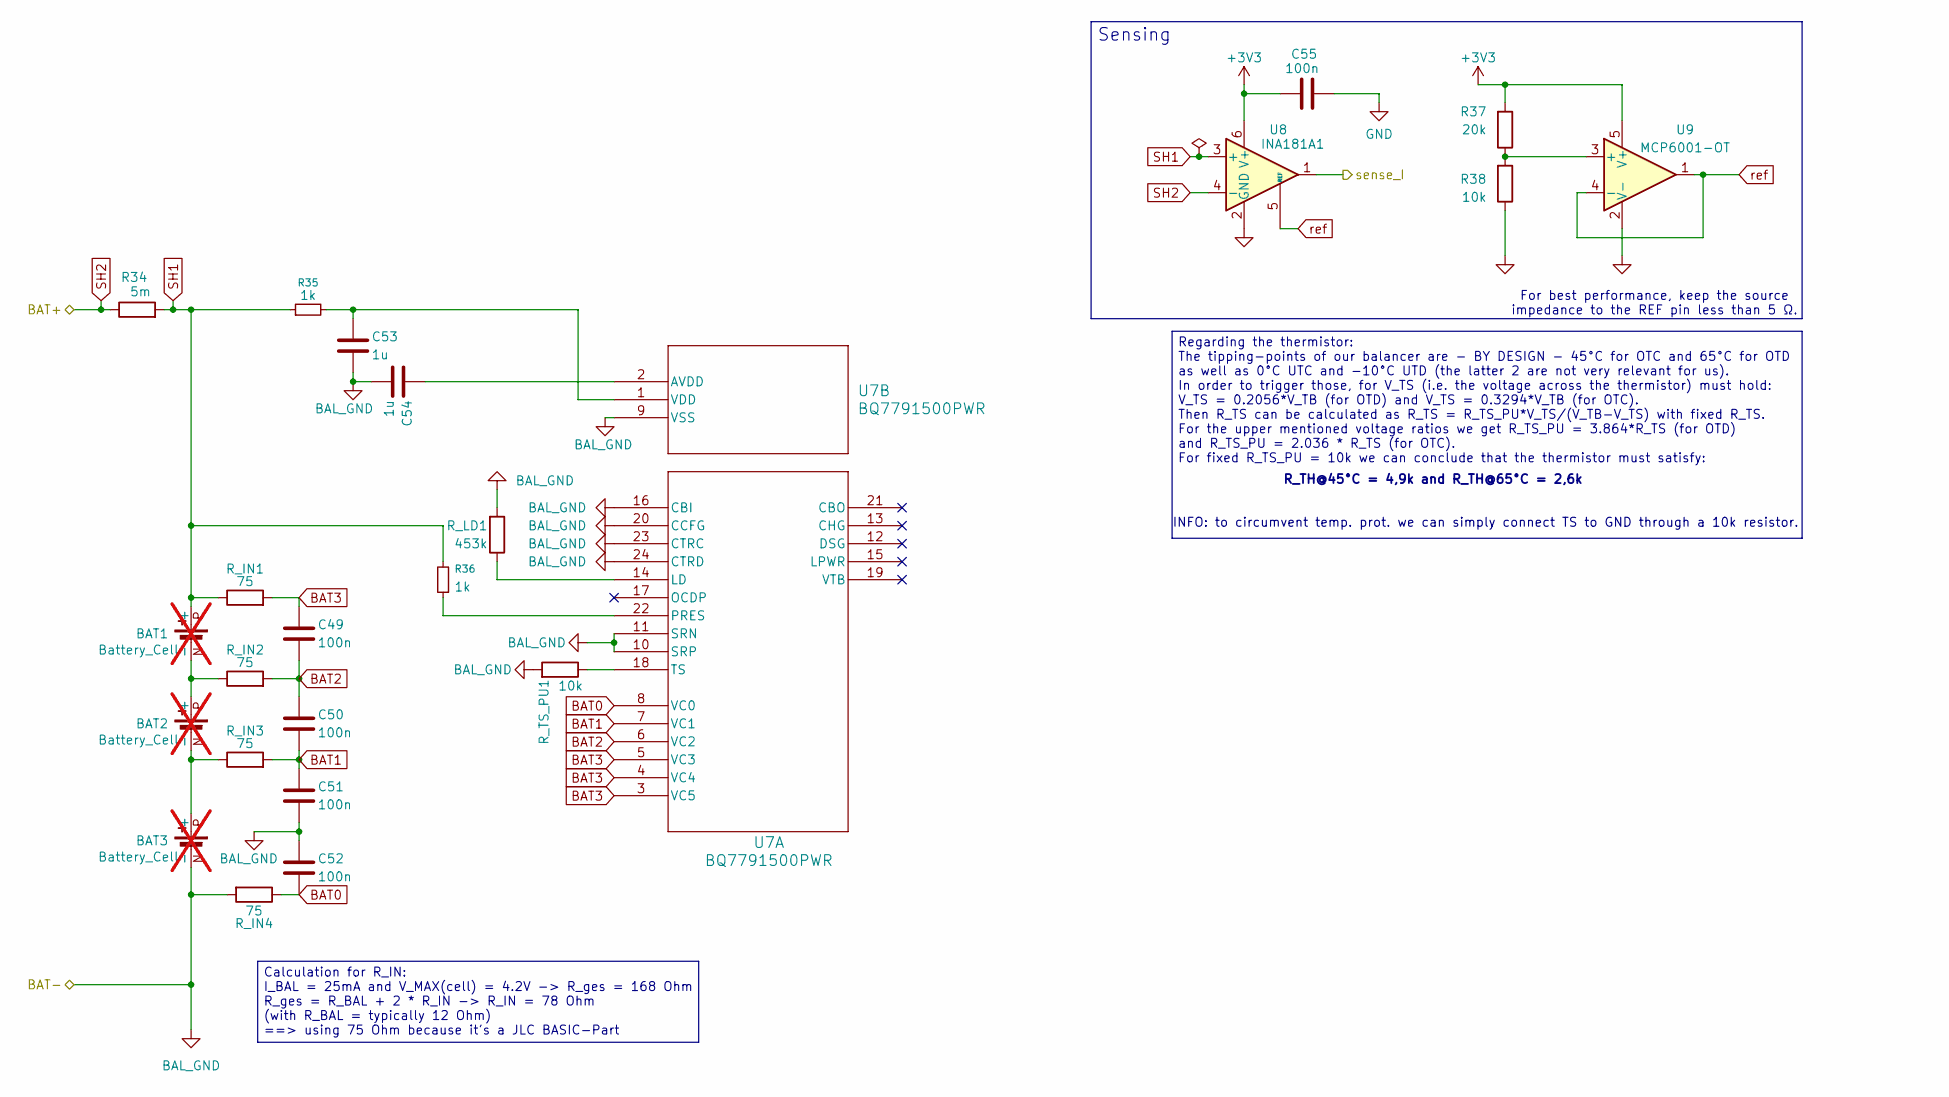
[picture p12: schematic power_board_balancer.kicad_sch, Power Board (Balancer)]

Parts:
BAT1, BAT2, BAT3: Battery_Cell; BAT_1043; LCSC x; not fitted
C49, C50, C51, C52: 100n; C_0402_1005Metric; LCSC C307331
C53, C54: 1u; C_0402_1005Metric; LCSC C52923
C55: 100n; C_0402_1005Metric; LCSC C1525
R34: 5m; R_2512_6332Metric_Pad1.40x3.35mm_HandSolder; Part# DSLR-K-3-5F; LCSC C41382686
R35, R36: 1k; R_0402_1005Metric; LCSC C11702
R37: 20k; R_0402_1005Metric_Pad0.72x0.64mm_HandSolder; LCSC C25765
R38: 10k; R_0402_1005Metric_Pad0.72x0.64mm_HandSolder; LCSC C25744
R_IN1, R_IN2, R_IN3, R_IN4: 75; R_0603_1608Metric; LCSC C4275
R_LD1: 453k; R_0402_1005Metric; LCSC C27009
R_TS_PU1: 10k; R_0402_1005Metric; LCSC C25744
U7: BQ7791500PWR; TSSOP-24_4.4x7.8mm_P0.65mm; LCSC C2876946
U8: INA181A1; SOT-23-6; LCSC C2058943
U9: MCP6001-OT; SOT-23-5; LCSC C116490

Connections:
+3V3: C55.1, R37.2, U8.6 (V+), U9.5 (V+); also elsewhere on the board
/Balancer/sense_I: U8.1; also elsewhere on the board
BAL_GND: BAT3.N (-), C51.2, C52.1, C53.2, C54.2, C55.2, R38.1, R_IN4.2, R_LD1.2, R_TS_PU1.2, U7.9 (VSS), U7.10 (SRP), U7.11 (SRN), U7.16 (CBI), U7.20 (CCFG), U7.23 (CTRC), U7.24 (CTRD), U8.2 (GND), U9.2 (V-); also elsewhere on the board
BAT0: C52.2, R_IN4.1, U7.8 (VC0)
BAT1: C50.2, C51.1, R_IN3.2, U7.7 (VC1)
BAT2: C49.2, C50.1, R_IN2.2, U7.6 (VC2)
BAT3: C49.1, R_IN1.2, U7.3 (VC5), U7.4 (VC4), U7.5 (VC3)
unnamed: BAT1.N (-), BAT2.P (+), R_IN2.1
unnamed: BAT2.N (-), BAT3.P (+), R_IN3.1
unnamed: R_LD1.1, U7.14 (LD)
unnamed: R36.1, U7.22 (PRES)
unnamed: R_TS_PU1.1, U7.18 (TS)
unnamed: C54.1, U7.2 (AVDD)
unnamed: C53.1, R35.2, U7.1 (VDD)
unnamed: R37.1, R38.2, U9.3 (+)
SH1: BAT1.P (+), R34.2, R35.1, R36.2, R_IN1.1, U8.3 (+)
V_BAT: R34.1, U8.4 (-); also elsewhere on the board
ref: U8.5 (REF), U9.1, U9.4 (-)

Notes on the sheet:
For best performance, keep the source impedance to the REF pin less than 5 Ω.
R_TH@45°C = 4,9k and R_TH@65°C = 2,6k
INFO: to circumvent temp. prot. we can simply connect TS to GND through a 10k resistor.
Calculation for R_IN: I_BAL = 25mA and V_MAX(cell) = 4.2V -> R_ges = 168 Ohm R_ges = R_BAL + 2 * R_IN -> R_IN = 78 Ohm (with R_BAL = typically 12 Ohm) ==> using 75 Ohm because it's a JLC BASIC-Part
Regarding the thermistor: The tipping-points of our balancer are - BY DESIGN - 45°C for OTC and 65°C for OTD as well as 0°C UTC and -10°C UTD (the latter 2 are not very relevant for us). In order to trigger those, for V_TS (i.e. the voltage across the thermistor) must hold: V_TS = 0.2056*V_TB (for 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
Sensing

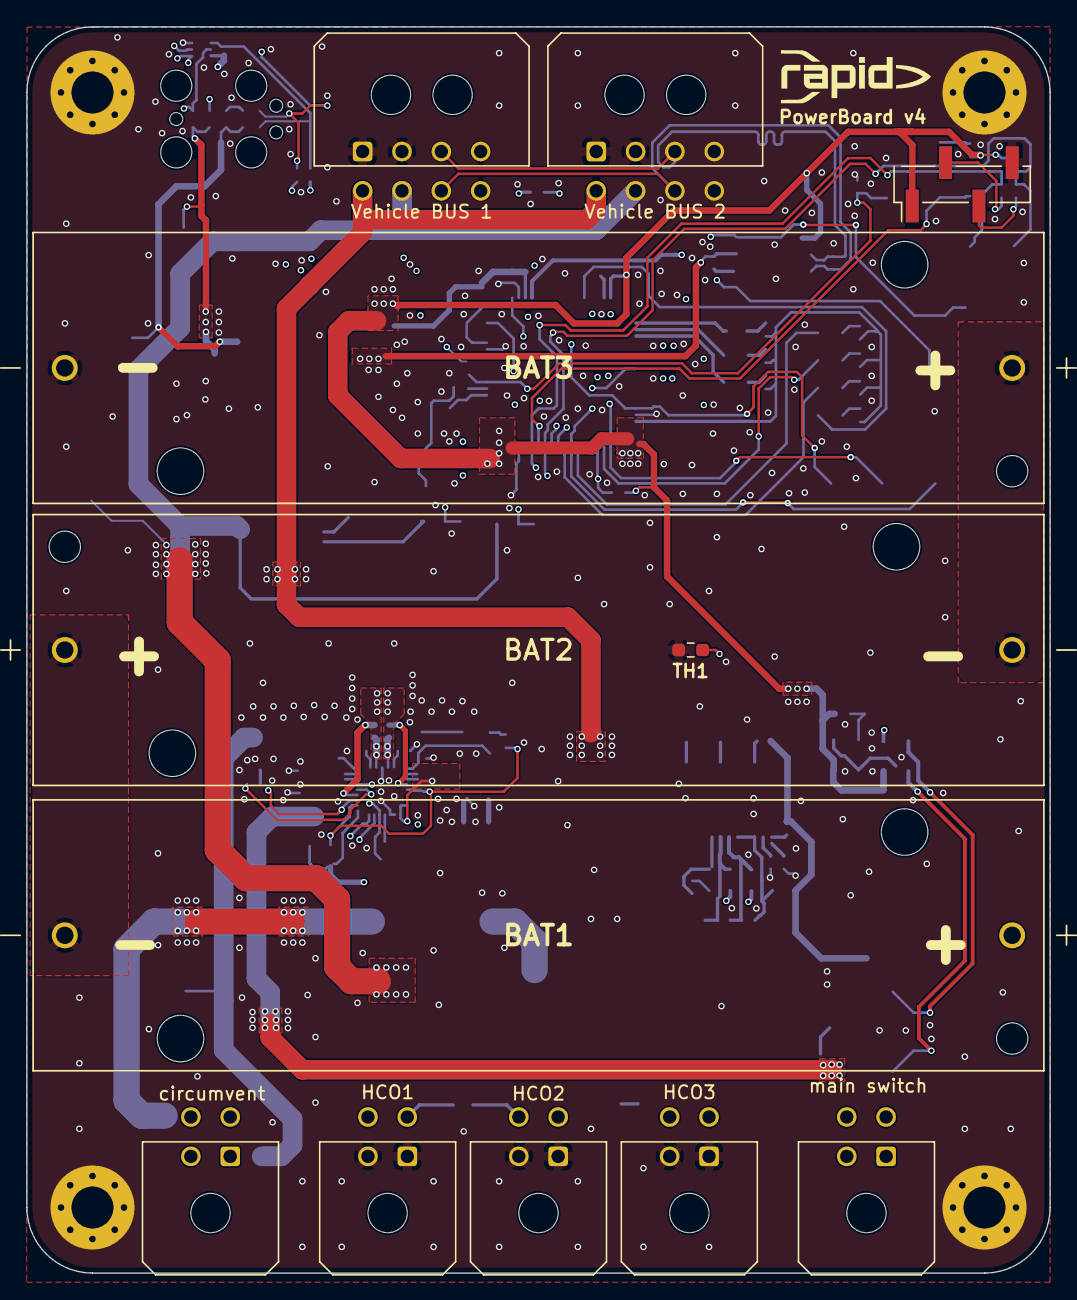
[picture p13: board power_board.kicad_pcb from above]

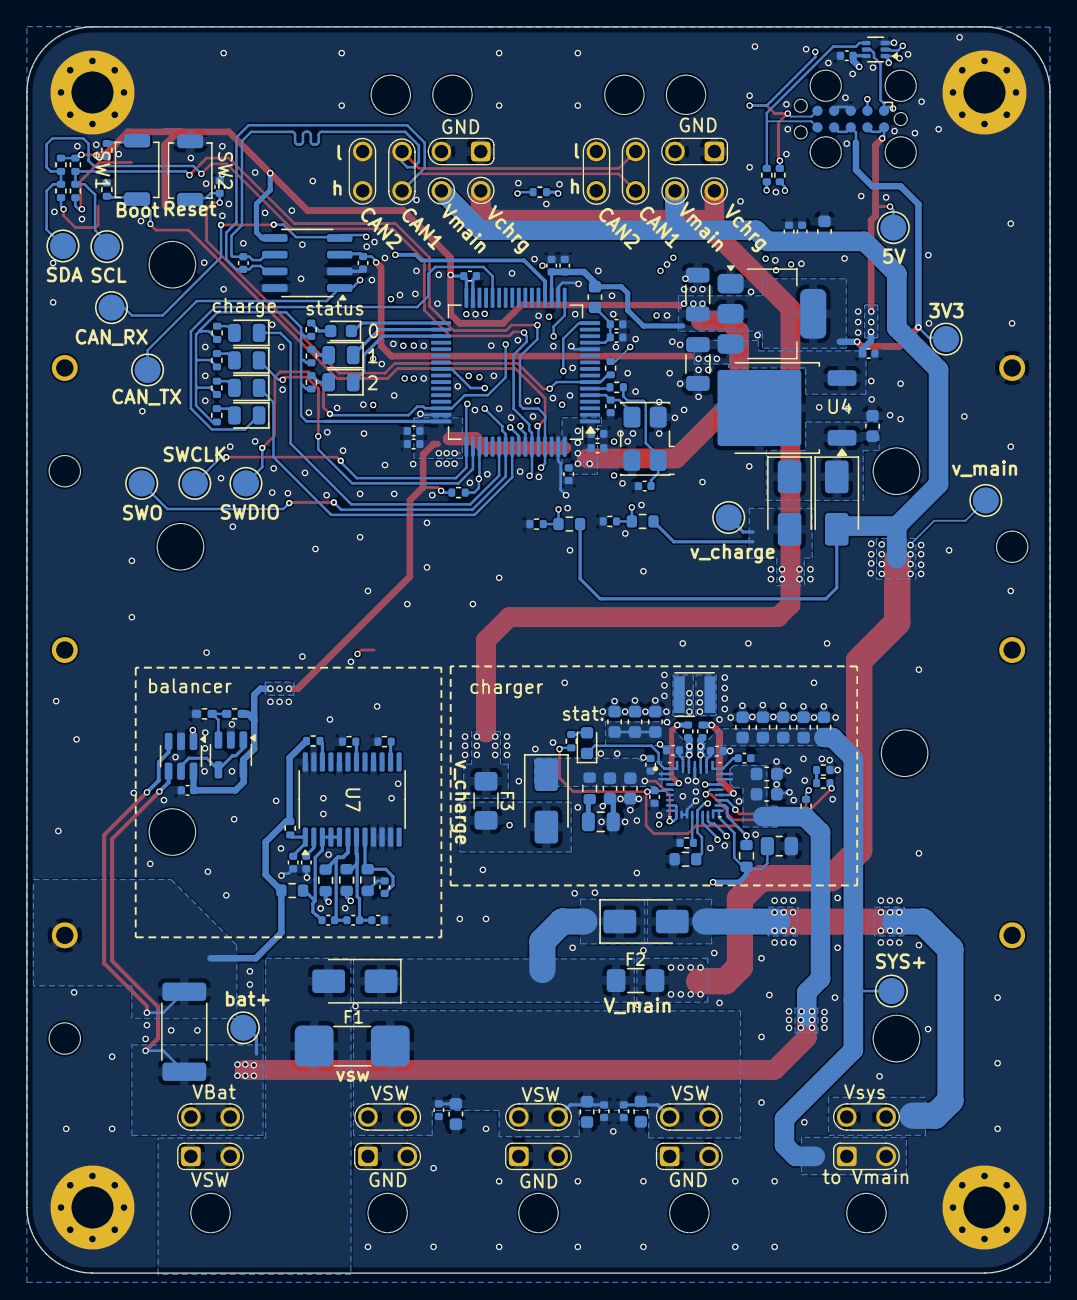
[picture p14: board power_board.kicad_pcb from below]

Board: 4 copper layers, 78.0 x 95.0 mm, 159 parts (143 on the bottom side), 86 nets.

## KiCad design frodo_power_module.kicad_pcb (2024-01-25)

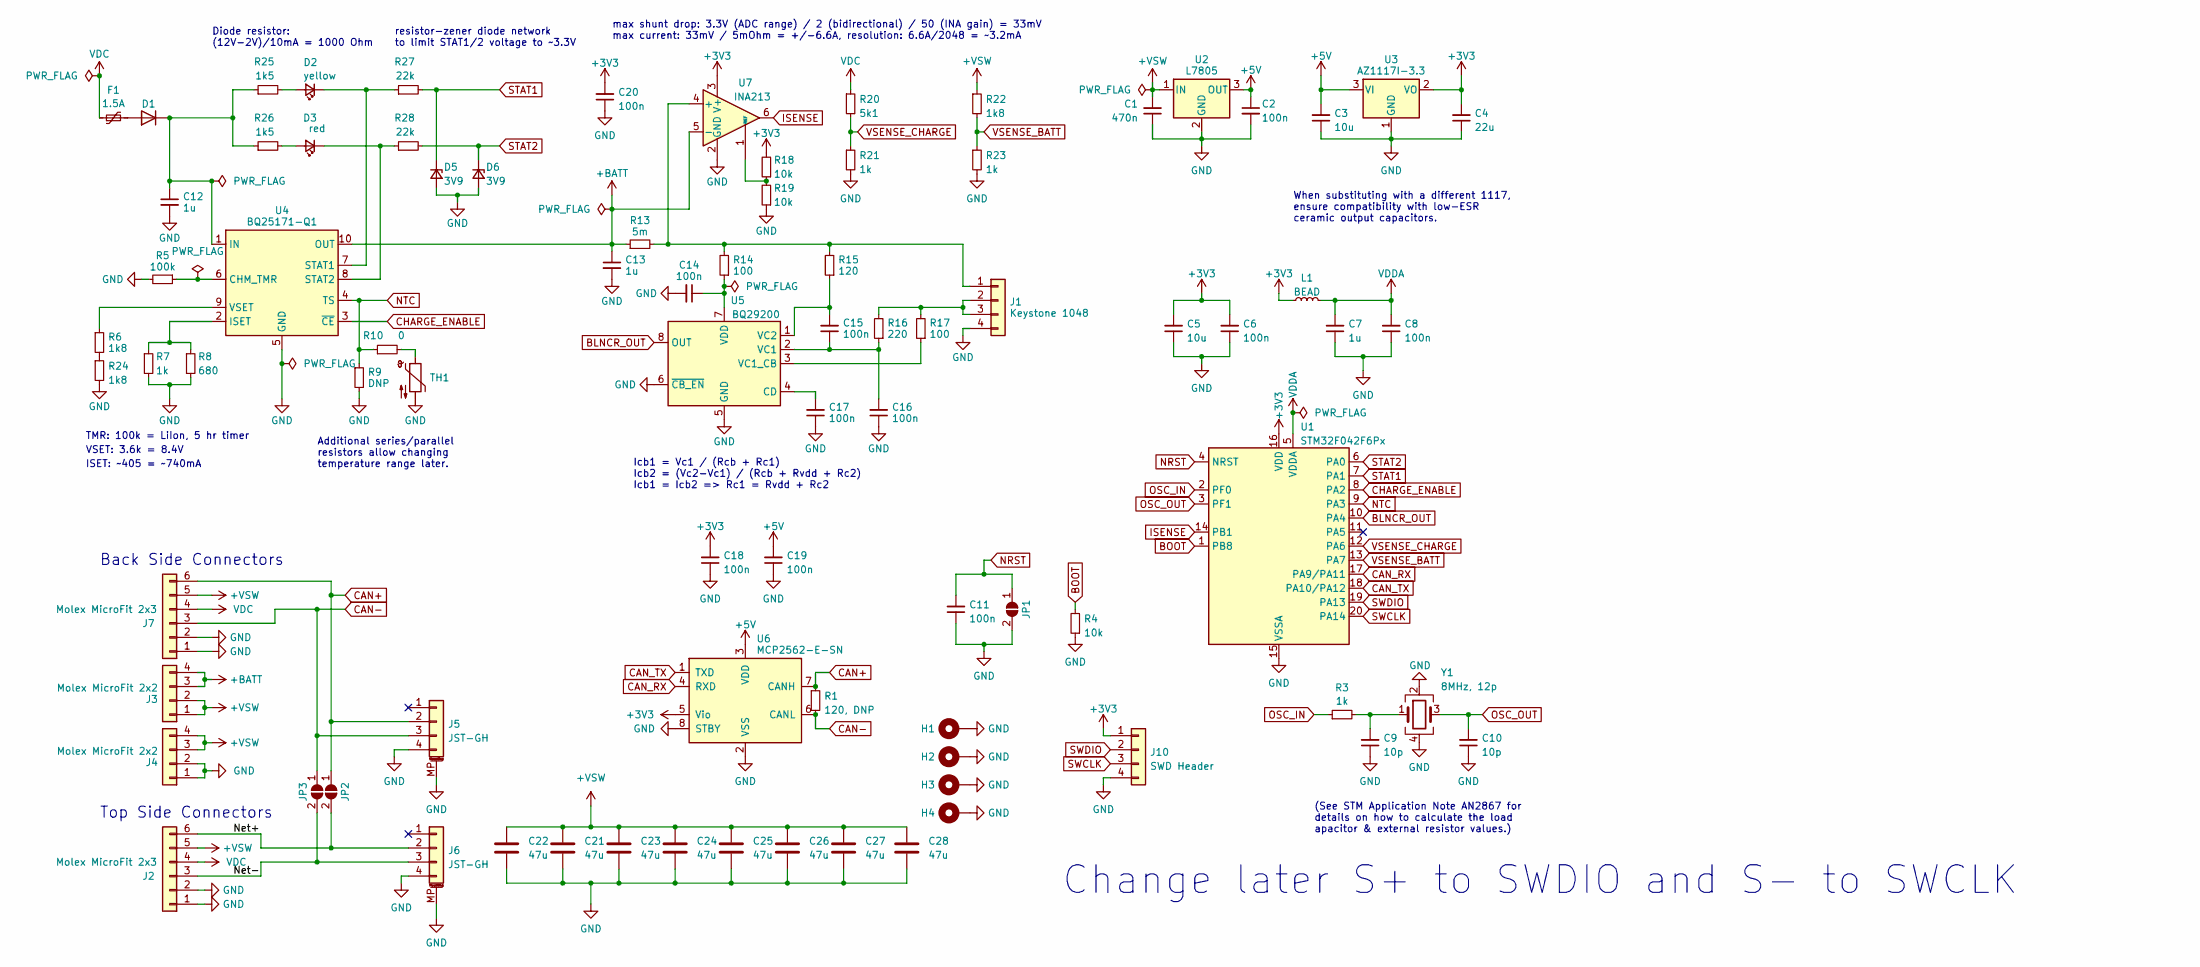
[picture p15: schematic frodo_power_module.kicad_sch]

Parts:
C1: 470n; C_0603_1608Metric; Part# CL10B474KA8NNNC; LCSC# C1623
C2, C6, C8, C11, C14, C15, C16, C17, C18, C19, C20: 100n; C_0603_1608Metric; Part# CC0603KRX7R9BB104; LCSC# C14663
C3, C5: 10u; C_1206_3216Metric; Part# CL31A106KBHNNNE; LCSC# C13585
C4: 22u; C_1206_3216Metric; Part# CL31A226KAHNNNE; LCSC# C12891
C7, C12, C13: 1u; C_0805_2012Metric; Part# CL21B105KBFNNNE; LCSC# C28323
C9, C10: 10p; C_0603_1608Metric; Part# CL10C100JB8NNNC; LCSC# C1634
C21, C22, C23, C24, C25, C26, C27, C28: 47u; C_1206_3216Metric
D1: D_SMA; Part# SS54; DigiKey# SK34A-LTPMSCT-ND
D2: yellow; LED_0603_1608Metric; Part# 19-213/Y2C-CQ2R2L/3T(CY); LCSC# C72038
D3: red; LED_0603_1608Metric; Part# KT-0603R; LCSC# C2286
D5, D6: 3V9; SOD323F_DIO; Part# D3Z3V9BF-7; LCSC# C444415
F1: 1.5A; Fuse_1206_3216Metric; Part# 0ZCJ0075AF2E; DigiKey# 507-1805-1-ND
H1, H2, H3, H4: MountingHole_Pad; MountingHole_3.2mm_M3_Pad_Via; Part# N/A; DigiKey# N/A
J1: Keystone 1048; keystone_1048; Part# 1048; DigiKey# 36-1098-ND
J2, J7: Molex MicroFit 2x3; Molex_Micro-Fit_3.0_43045-0600_2x03_P3.00mm_Horizontal; Part# 0430450600; LCSC# C127367
J3, J4: Molex MicroFit 2x2; Molex_Micro-Fit_3.0_43045-0400_2x02_P3.00mm_Horizontal; Part# 0430450400; LCSC# C122413
J5, J6: JST-GH; JST_GH_SM04B-GHS-TB_1x04-1MP_P1.25mm_Horizontal; Part# SM04B-GHS-TB; LCSC# C189895
J10: SWD Header; PinHeader_1x04_P2.54mm_Vertical; Part# N/A; DigiKey# N/A
JP1, JP2, JP3: r; SolderJumper-2_P1.3mm_Open_RoundedPad1.0x1.5mm; Part# N/A; DigiKey# N/A
L1: BEAD; L_0603_1608Metric; Part# GZ1608D601TF; LCSC# C1002
R1: 120, DNP; R_0603_1608Metric; Part# 0603WAF1200T5E; LCSC# C22787
R3, R7, R21, R23: 1k; R_0603_1608Metric; Part# 0603WAF1001T5E; LCSC# C21190
R4, R18, R19: 10k; R_0603_1608Metric; Part# 0603WAF1002T5E; LCSC# C25804
R5: 100k; R_0603_1608Metric; Part# 0603WAF1003T5E; LCSC# C25803
R6, R22, R24: 1k8; R_0603_1608Metric; Part# 0603WAF1801T5E; LCSC# C4177
R8: 680; R_0603_1608Metric; Part# 0603WAF6800T5E; LCSC# C23228
R9: DNP; R_0603_1608Metric; Part# N/A; LCSC# N/A
R10: 0; R_0603_1608Metric; Part# 0603WAF0000T5E; LCSC# C21189
R13: 5m; R_2512_6332Metric; Part# PA2512FKE7W0R005E; LCSC# C723630
R14, R17: 100; R_0603_1608Metric; Part# 0603WAF1000T5E; LCSC# C22775
R15: 120; R_0603_1608Metric; Part# 0603WAF1200T5E; LCSC# C22787
R16: 220; R_0603_1608Metric; Part# 0603WAF2200T5E; LCSC# C22962
R20: 5k1; R_0603_1608Metric; Part# 0603WAF5101T5E; LCSC# C23186
R25, R26: 1k5; R_0603_1608Metric; Part# 0603WAF1501T5E; LCSC# C22843
R27, R28: 22k; R_0603_1608Metric; Part# 0603WAF2202T5E; LCSC# C31850
TH1: NCU18XH103F6SRB; R_0603_1608Metric; Part# NCU18XH103F6SRB; DigiKey# 490-18139-1-ND
U1: STM32F042F6Px; TSSOP-20_4.4x6.5mm_P0.65mm; Part# STM32F042F6P6TR; DigiKey# 497-19656-1-ND
U2: L7805; TO-252-2; Part# L78M05ABDT-TR; LCSC# C58069
U3: AZ1117I-3.3; SOT-223-3_TabPin2; Part# AZ1117CH-3.3TRG1; LCSC# C92102
U4: BQ25171-Q1; Texas_S-PVSON-N10_ThermalVias; Part# BQ25171QWDRCRQ1; DigiKey# 296-BQ25171QWDRCRQ1CT-ND
U5: BQ29200; Texas_S-PVSON-N8_ThermalVias; Part# BQ29200DRBT; DigiKey# 296-32038-1-ND
U6: MCP2562-E-SN; SOIC-8_3.9x4.9mm_P1.27mm; Part# MCP2562-H/SN; DigiKey# MCP2562-H/SN
U7: INA213; SOT-363_SC-70-6; Part# INA213AIDCKR; DigiKey# 296-26072-1-ND
Y1: 8MHz, 12p; Crystal_SMD_5032-4Pin_5.0x3.2mm; Part# 5TJ480000NYLBC; DigiKey# 50-ECS-80-12-33-JGN-CT-ND

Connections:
+3V3: C4.2, C5.2, C6.2, C18.2, C20.2, J10.1, L1.1, R18.2, U1.16 (VDD), U3.2 (VO), U6.5 (Vio), U7.3 (V+)
+5V: C2.1, C3.2, C19.2, U2.3 (OUT), U3.3 (VI), U6.3 (VDD)
+BATT: C13.1, J3.3, J3.4, R13.1, U4.10 (OUT), U7.5 (-)
+VSW: C1.2, C21.1, C22.1, C23.1, C24.1, C25.1, C26.1, C27.1, C28.1, J2.5, J3.1, J3.2, J4.3, J4.4, J7.5, R22.1, U2.1 (IN)
/Net+: J2.6, J6.2, JP2.2 (B)
/Net-: J2.3, J6.3, JP3.2 (B)
BLNCR_OUT: U1.10 (PA4), U5.8 (OUT)
BOOT: R4.2, U1.1 (PB8)
CAN+: J5.2, J7.6, JP2.1 (A), R1.1, U6.7 (CANH)
CAN-: J5.3, J7.3, JP3.1 (A), R1.2, U6.6 (CANL)
CAN_RX: U1.17 (PA9/PA11), U6.4 (RXD)
CAN_TX: U1.18 (PA10/PA12), U6.1 (TXD)
CHARGE_ENABLE: U1.8 (PA2), U4.3 (~CE)
GND: C1.1, C2.2, C3.1, C4.1, C5.1, C6.1, C7.1, C8.1, C9.1, C10.1, C11.1, C12.2, C13.2, C14.2, C16.1, C17.1, C18.1, C19.1, C20.1, C21.2, C22.2, C23.2, C24.2, C25.2, C26.2, C27.2, C28.2, D5.2 (A), D6.2 (A), H1.1, H2.1, H3.1, H4.1, J1.4, J2.1, J2.2, J4.1, J4.2, J5.4, J5.MP (MountPin), J6.4, J6.MP (MountPin), J7.1, J7.2, J10.4, JP1.2 (B), R4.1, R5.2, R7.2, R8.2, R9.2, R19.1, R21.2, R23.2, R24.2, TH1.2, U1.15 (VSSA), U2.2 (GND), U3.1 (GND), U4.5 (GND), U4.11 (GND), U5.5 (GND), U5.6 (~CB_EN), U5.9 (PWR_PAD), U6.2 (VSS), U6.8 (STBY), U7.2 (GND), Y1.2, Y1.4
ISENSE: U1.14 (PB1), U7.6
NRST: C11.2, JP1.1 (A), U1.4 (NRST)
NTC: R9.1, R10.1, U1.9 (PA3), U4.4 (TS)
unnamed: C9.2, R3.2, Y1.1
unnamed: D1.2 (A), F1.2
unnamed: C12.1, D1.1 (K), R25.1, R26.1, U4.1 (IN)
unnamed: D2.2 (A), R25.2
unnamed: D2.1 (K), R27.1, U4.7 (STAT1)
unnamed: D3.2 (A), R26.2
unnamed: D3.1 (K), R28.1, U4.8 (STAT2)
unnamed: J1.1, R13.2, R14.2, R15.2, U7.4 (+)
unnamed: J1.2, J1.3, R16.2, R17.2
unnamed: R10.2, TH1.1
unnamed: R6.2, R24.1
unnamed: R5.1, U4.6 (CHM_TMR)
unnamed: R7.1, R8.1, U4.2 (ISET)
unnamed: R6.1, U4.9 (VSET)
unnamed: C17.2, U5.4 (CD)
unnamed: C15.1, C16.2, R16.1, U5.2 (VC1)
unnamed: R17.1, U5.3 (VC1_CB)
unnamed: C15.2, R15.1, U5.1 (VC2)
unnamed: C14.1, R14.1, U5.7 (VDD)
unnamed: R18.1, R19.2, U7.1 (REF)
OSC_IN: R3.1, U1.2 (PF0)
OSC_OUT: C10.2, U1.3 (PF1), Y1.3
STAT1: D5.1 (K), R27.2, U1.7 (PA1)
STAT2: D6.1 (K), R28.2, U1.6 (PA0)
SWCLK: J10.3, U1.20 (PA14)
SWDIO: J10.2, U1.19 (PA13)
VDC: F1.1, J2.4, J7.4, R20.1
VDDA: C7.2, C8.2, L1.2, U1.5 (VDDA)
VSENSE_BATT: R22.2, R23.1, U1.13 (PA7)
VSENSE_CHARGE: R20.2, R21.1, U1.12 (PA6)

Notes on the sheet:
(See STM Application Note AN2867 for details on how to calculate the load apacitor & external resistor values.)
Diode resistor: (12V-2V)/10mA = 1000 Ohm
Icb1 = Vc1 / (Rcb + Rc1) Icb2 = (Vc2-Vc1) / (Rcb + Rvdd + Rc2) Icb1 = Icb2 => Rc1 = Rvdd + Rc2
When substituting with a different 1117, ensure compatibility with low-ESR ceramic output capacitors.
max shunt drop: 3.3V (ADC range) / 2 (bidirectional) / 50 (INA gain) = 33mV max current: 33mV / 5mOhm = +/-6.6A, resolution: 6.6A/2048 = ~3.2mA
TMR: 100k = LiIon, 5 hr timer
Top Side Connectors
Back Side Connectors
VSET: 3.6k = 8.4V
Change later S+ to SWDIO and S- to SWCLK
Additional series/parallel resistors allow changing temperature range later.
ISET: ~405 = ~740mA
resistor-zener diode network to limit STAT1/2 voltage to ~3.3V

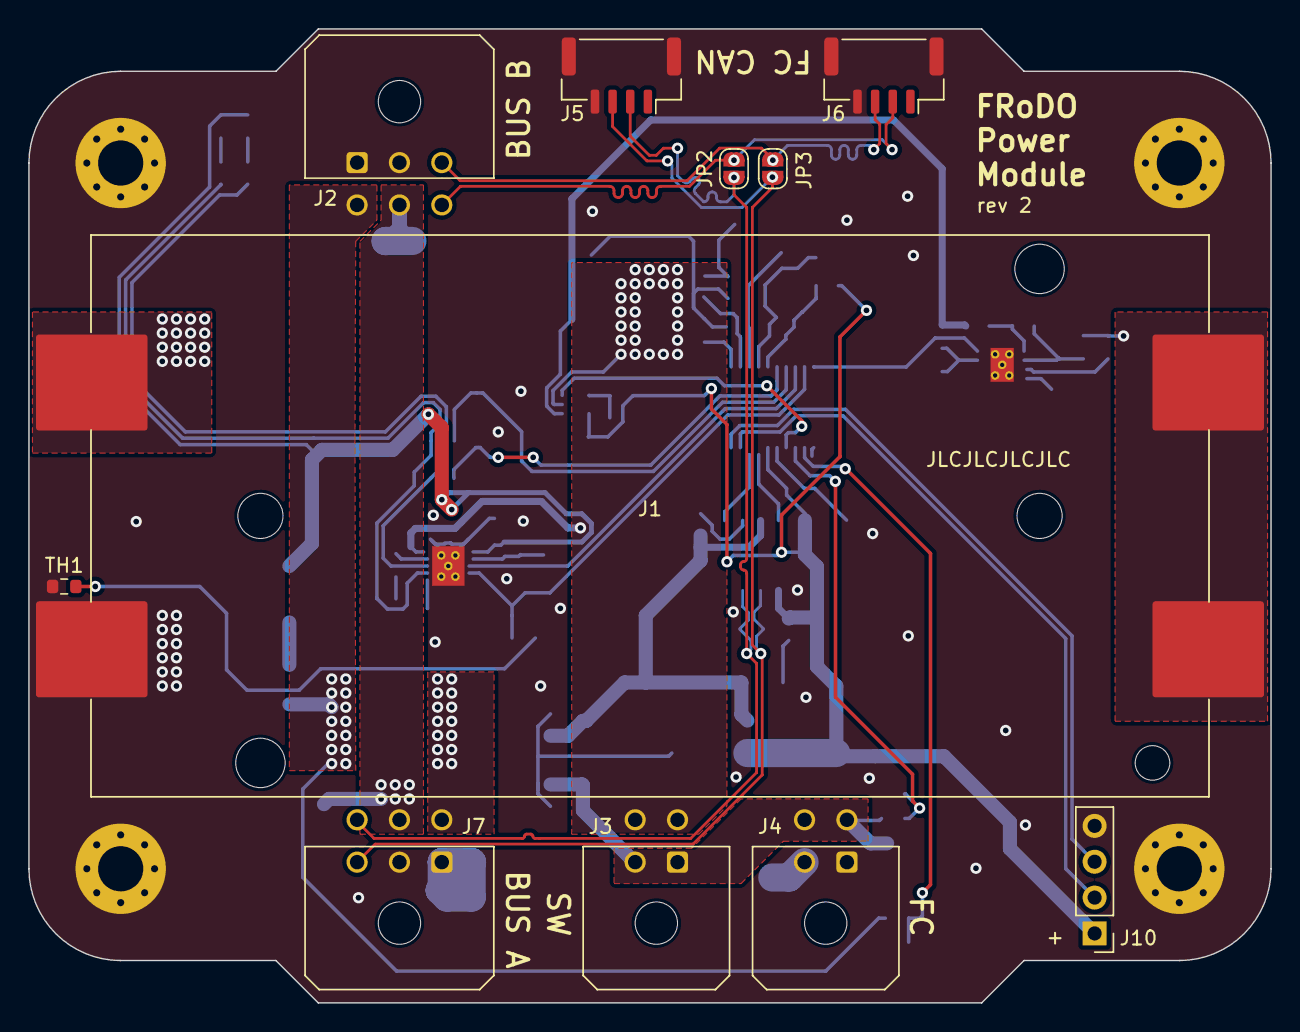
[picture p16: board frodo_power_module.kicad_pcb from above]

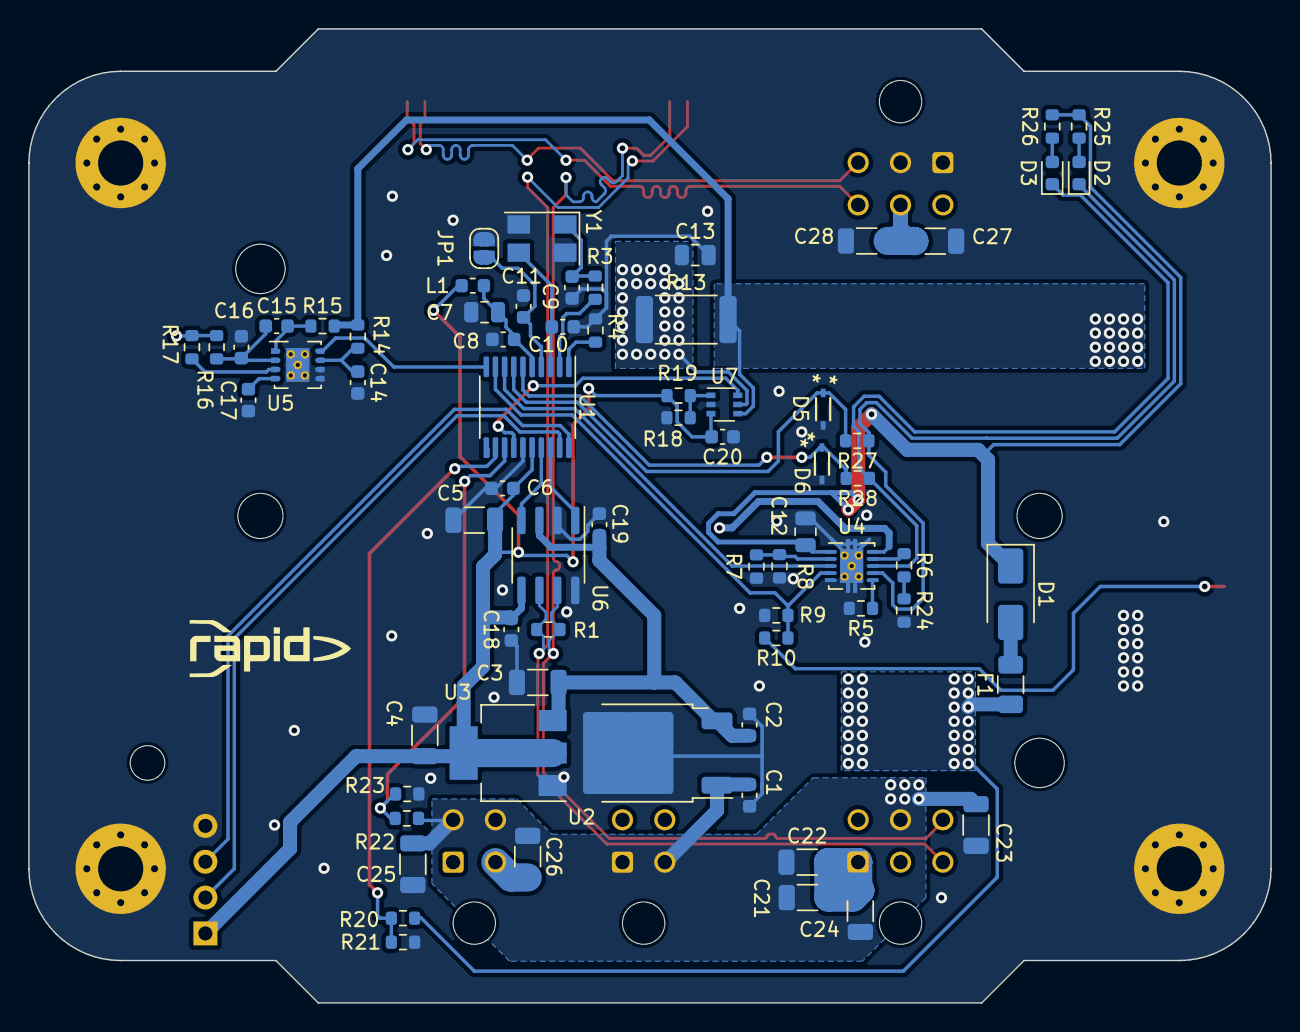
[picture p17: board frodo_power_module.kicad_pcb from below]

Board: 2 copper layers, 88.0 x 69.0 mm, 84 parts (69 on the bottom side), 47 nets.

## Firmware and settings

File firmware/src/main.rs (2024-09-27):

#![no_std]
#![no_main]

use defmt::*;
use {defmt_rtt as _, panic_probe as _};

use embassy_executor::Spawner;
use embassy_stm32::adc::{Adc, SampleTime};
use embassy_stm32::{bind_interrupts, Config};
use embassy_stm32::can::bxcan::{Frame, StandardId};
use embassy_stm32::can::{Can, Rx0InterruptHandler, Rx1InterruptHandler, SceInterruptHandler, TxInterruptHandler};
use embassy_stm32::gpio::{Input, Pull};
use embassy_stm32::pac::SYSCFG;
use embassy_stm32::peripherals::CAN;
use embassy_stm32::time::Hertz;
use embassy_time::{Delay, Duration, Ticker};

use shared_types::can::*;

const MEASUREMENT_FREQUENCY_HZ: u64 = 5;

bind_interrupts!(struct Irqs {
    ADC1 => embassy_stm32::adc::InterruptHandler<embassy_stm32::peripherals::ADC>;
    CEC_CAN => Rx0InterruptHandler<CAN>, Rx1InterruptHandler<CAN>, SceInterruptHandler<CAN>, TxInterruptHandler<CAN>;
});

fn to_millivolts(vref_sample: u16, sample: u16) -> u32 {
    // From https://www.st.com/resource/en/datasheet/stm32f031c6.pdf
    // 6.3.4 Embedded reference voltage
    const VREFINT_MV: u32 = 1230; // mV
    u32::from(sample) * VREFINT_MV / u32::from(vref_sample)
}

#[embassy_executor::main]
async fn main(_spawner: Spawner) {
    let mut config: Config = Default::default();
    config.rcc.hse = Some(Hertz::mhz(8));
    config.rcc.sys_ck = Some(Hertz::mhz(48));

    let p = embassy_stm32::init(config);

    SYSCFG.cfgr1().modify(|w| w.set_pa11_pa12_rmp(true));

    let mut adc = Adc::new(p.ADC, Irqs, &mut Delay);
    adc.set_sample_time(SampleTime::Cycles239_5);

    let mut vref = adc.enable_vref(&mut Delay);
    let vref_sample = adc.read(&mut vref).await;

    let stat1 = Input::new(p.PA1, Pull::None);
    let stat2 = Input::new(p.PA0, Pull::None);
    let mut vsense_charge = p.PA6;
    let mut vsense_batt = p.PA7;
    let mut isense = p.PB1;

    let mut can = Can::new(p.CAN, p.PA11, p.PA12, Irqs);

    // We don't want to receive anything.
    can.as_mut()
        .modify_filters()
        .clear();

    can.as_mut()
        .modify_config()
        .set_loopback(false) // Receive own frames
        .set_silent(false)
        .set_automatic_retransmit(false)
        .leave_disabled();

    can.set_bitrate(125_000);

    can.enable().await;

    let can_message_id = CanBusMessageId::BatteryBoardInput(0);
    let standard_id = StandardId::new(can_message_id.into()).unwrap();

    let mut ticker = Ticker::every(Duration::from_hz(MEASUREMENT_FREQUENCY_HZ));

    loop {
        let voltage_charge = (to_millivolts(vref_sample, adc.read(&mut vsense_charge).await) as f32 * (6.1 / 1.0)) as u16;
        let voltage_battery = (to_millivolts(vref_sample, adc.read(&mut vsense_batt).await) as f32 * (2.8 / 1.0)) as u16;
        let current_raw = (to_millivolts(vref_sample, adc.read(&mut isense).await) as i16) - 1650;
        let current = ((current_raw as f32) / (50.0 * 0.005)) as i32;

        info!("{}, {}, {}", voltage_charge, voltage_battery, current);

        let msg = BatteryTelemetryMessage {
            voltage_battery,
            voltage_charge,
            current,
            stat0: stat1.is_high(),
            stat1: stat2.is_high() // TODO
        }.serialize_with_crc();

        let tx_frame = Frame::new_data(standard_id, msg);

        can.write(&tx_frame).await;
        can.flush_all().await;

        ticker.next().await;
    }
}

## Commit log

2023-06-30 Add battery IC circuits
    [frodo_power_module.kicad_sch]
2023-06-30 Update PCB
    [frodo_power_module.kicad_pcb, frodo_power_module.kicad_sch]
2023-07-01 Fixed VSET for charger
    [frodo_power_module.kicad_sch]
2023-07-02 add current sense amp
    [frodo_power_module.kicad_sch]
2023-07-02 created component groups on pcb
    [frodo_power_module.kicad_pcb, frodo_power_module.kicad_sch]
2023-07-05 Add current sense amp to PCB
    [frodo_power_module.kicad_pcb, frodo_power_module.kicad_sch]
2023-07-09 changed PCB
    [frodo_power_module.kicad_pcb, frodo_power_module.kicad_sch]
2023-07-12 Update PCB design, add LEDs
    [430450400.step, frodo_power_module.kicad_pcb, frodo_power_module.kicad_sch]
2023-07-17 Add fuses to outputs, finish BOM
    [frodo_power_module.kicad_pcb, frodo_power_module.kicad_sch]
2023-11-07 removed breakwire system
    [frodo_power_module.kicad_sch]
2023-11-08 removed breakwire and changed Iset resistance from 440 to 390 to achieve approx 800mA charging
    [frodo_power_module.kicad_sch]
2023-12-03 modified schematic
    [frodo_power_module.kicad_sch]
2023-12-04 changed battery connector type, removed breakwrie, Iset resisrtor config and placed LEDS on main power supply
    [frodo_power_module.kicad_sch]
2023-12-04 removed other connectors
    [frodo_power_module.kicad_sch]
2023-12-05 Add review comments
    [frodo_power_module.kicad_sch]
2023-12-08 Review: Added resistor-zener diode network to limit voltage to STAT1/2 to ~3.3V
    [frodo_power_module.kicad_sch]
2023-12-11 changed connector Bezeichnet due to conflicts and made Keytore 1048 pads little bit bigger
    [frodo_power_module.kicad_sch]
2023-12-13 added power flags for ERC and removed all errors
    [frodo_power_module.kicad_sch]
2023-12-14 added footprints to D5 D7 J2 and J7. Needs review
    [frodo_power_module.kicad_sch]
2023-12-16 worked on pcb
    [frodo_power_module.kicad_pcb, frodo_power_module.kicad_sch]
2023-12-22 changed molex footprint from vertical to horiztontal
    [frodo_power_module.kicad_sch]
2023-12-23 Added Power Traces and made CAN+ and CAN- equal size
    [frodo_power_module.kicad_pcb, frodo_power_module.kicad_sch]
2023-12-23 worked on file
    [frodo_power_module.kicad_pcb, frodo_power_module.kicad_sch]
2023-12-23 saving work status
    [frodo_power_module.kicad_pcb, frodo_power_module.kicad_sch]
2023-12-23 saving work. Almost all routing is done. Ground plane will be added in the next steps to remove all errors and then the goal is to remove all warnings
    [SOD323F_DIO.step, frodo_power_module.kicad_pcb, frodo_power_module.kicad_sch]
2023-12-23 Only warning left to be removed. Also Jumper needs to be implemented and size or width of battery holder needs to be changed
    [frodo_power_module.kicad_pcb]
2023-12-24 changed PIN layout to suggested one
    [frodo_power_module.kicad_pcb, frodo_power_module.kicad_sch]
2023-12-31 DRC check for hole to hole clerance and minimum trace to trace clearance also changed a few traces and zones
    [frodo_power_module.kicad_pcb]
2023-12-31 changed zones
    [frodo_power_module.kicad_pcb]
2024-01-10 Minor trace tweaks
    [frodo_power_module.kicad_pcb, frodo_power_module.kicad_sch]
2024-01-11 clear DRC msgs, align elements to grid
    After updating the design constraints according to the JLCPCB manufacturing capabilities, the PTHs
    of component U5 were to small (0.25mm diameter, min. is 0.3mm). Note that after resolving this error,
    the DRC now shows a warning about a modified footprint of U5.
    [frodo_power_module.kicad_pcb]
2024-01-18 Replace parts with JLCPCB basic ones where possible, replace crystal footprint
    [frodo_power_module.kicad_pcb, frodo_power_module.kicad_sch]
2024-01-21 Minor routing changes, add outline
    [frodo_power_module.kicad_pcb]
2024-01-25 added capacitors. By updating pcb the old Osci footprint was restored. This needs to be changed
    [frodo_power_module.kicad_pcb, frodo_power_module.kicad_sch]
2024-01-25 Add finishing touches, generate fabrication files
    [frodo_power_module.csv, frodo_power_module.kicad_pcb, frodo_power_module.kicad_sch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]
2024-02-01 Finalize BOM, CPL
    [frodo_power_module-bottom-pos.csv]
2024-09-27 Correct battery current CAN message type
    [main.rs]
